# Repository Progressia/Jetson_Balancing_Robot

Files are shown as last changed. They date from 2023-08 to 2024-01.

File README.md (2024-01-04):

# JETSON BALANCING ROBOT

A two-wheeled balancing robot inspired by the [*SimpleFOC Balancing Robot*](https://github.com/simplefoc/Arduino-FOC-balancer.git)

<p align="center">
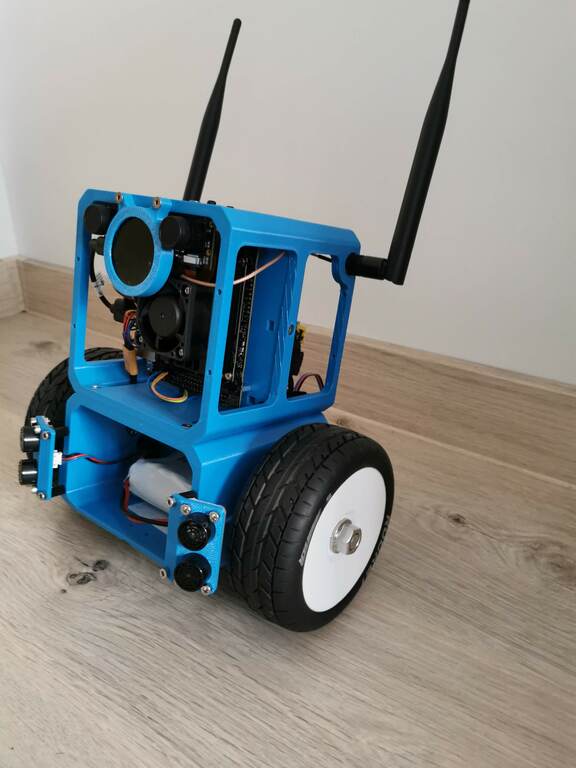
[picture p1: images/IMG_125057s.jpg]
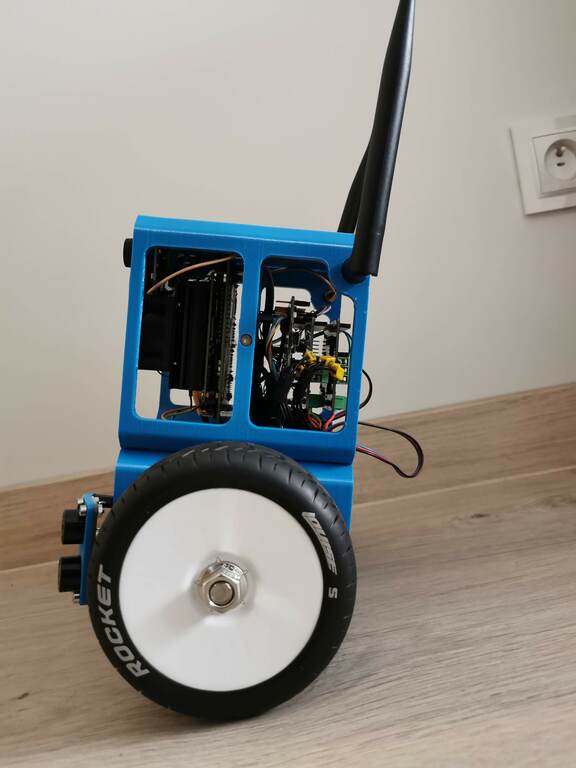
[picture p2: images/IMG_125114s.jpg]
  </p>

Modular two wheeled balancing robot based on gimbal BLDC motors and [*Simple**FOC**Shields*](https://simplefoc.com/). NVIDIA Jetson Nano is use  to allow for control motion on base computer vision algorithms and AI models. Application for remote control of robot was build on flutter framework. 3D models with STL files are in CAD folder.

## YouTube video demo

ToDo: Video -- comming soon

## Readme structure
- [Mechanical components](#mechanical-components)
    - [3D printed parts](#3d-printed-parts)
    - [Hardware parts](#hardware-parts)
- [Electrical components](#electrical-components)
    - [Structure](#structure)
    - [BLDC motor](#bldc-motor)
    - [Position sensors](#position-sensors)
    - [BLDC driver](#bldc-driver)
    - [IMU module](#imu-module)
    - [WiFi module](#wifi-module)
    - [Microcontroller](#microcontroller)
- [Software](#software)
    - [STM32 Code](#stm32-code)
    - [NVIDIA Jetson Nano Code](#nvidia-jetson-nano-code)
    - [Remote control app](#remote-control-app)
    - [RP2040 LCD UART](#rp2040-lcd-uart)

--------------------------

## Mechanical components

### 3D printed parts

Robot has 4 3d printed parts. You can find them in the `CAD` directory. They are (***reasonably precise***):
- Base frame (`base_frame.stl`)
- Cube frame (`cube_frame.stl`) 
- Plate for electronics (`plate.stl`)
- Wheel hub (`wheel_hub.stl`)
- Camera and LCD hub (`camera_lcd_hub.stl`)
- RP2040 LCD adapter (`rp2040_hub.stl`)
- Distance sensor hub (`dist_sens_hub.stl`)

Parts was printed from ABS filament.

>Beware: Assembly holes match the motor and electronics I was using, so please check the dimensions of your parts holes before printing

### Hardware parts

In addition to the printed parts, you will need two RC wheels (HEX17) and a handful of nuts and bolts

Component | Description
---- | ----
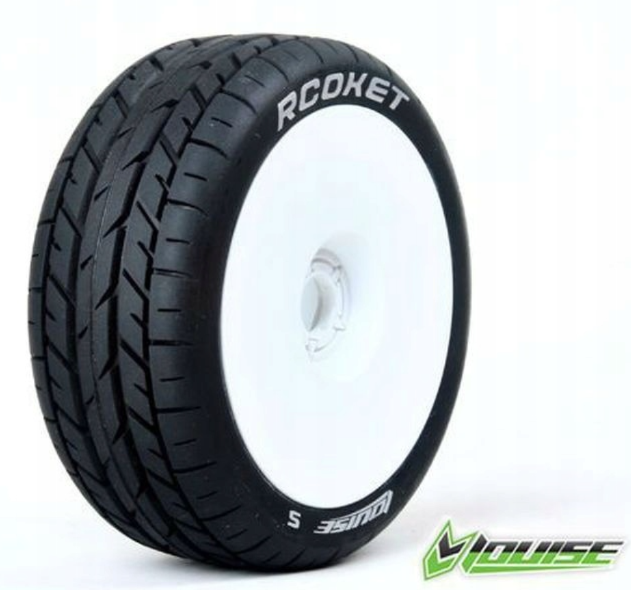
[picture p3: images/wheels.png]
 | Wheels Louise B-Rocket hex 17mm 1:8 Buggy (2 pcs)
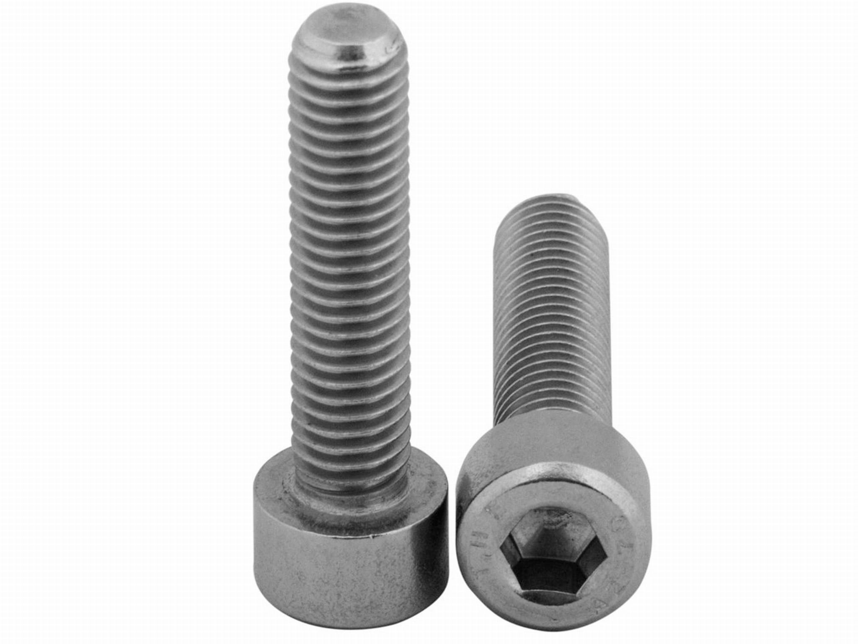
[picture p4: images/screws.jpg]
 | Screws M3x20 (4 pcs)
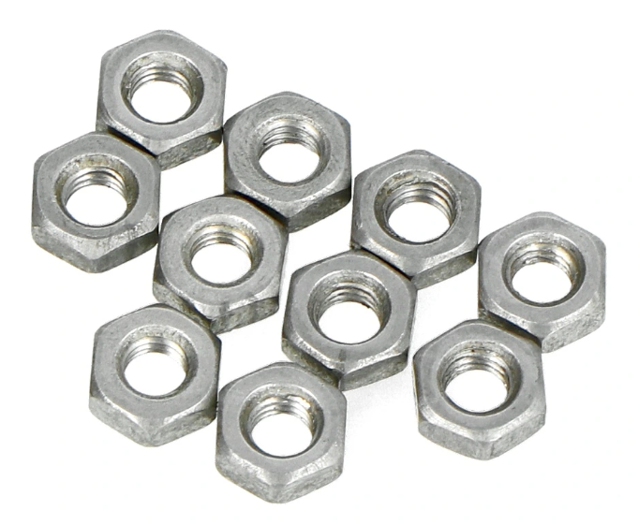
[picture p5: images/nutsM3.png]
 | Nuts M3 
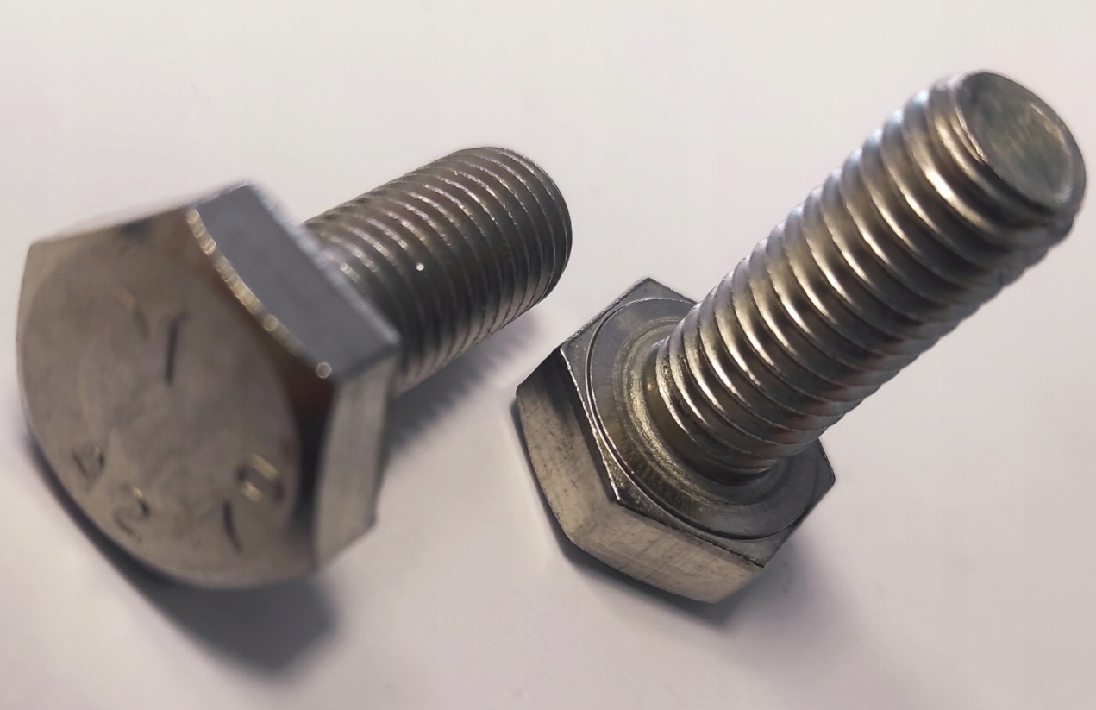
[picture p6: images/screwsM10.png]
 | Screws M10x25 (2 pcs)
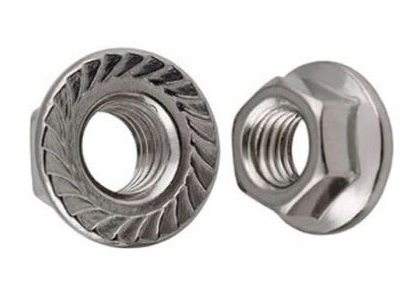
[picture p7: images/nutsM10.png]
  | Nuts M10 (2 pcs)

--------------------------

## Electrical components

### Structure
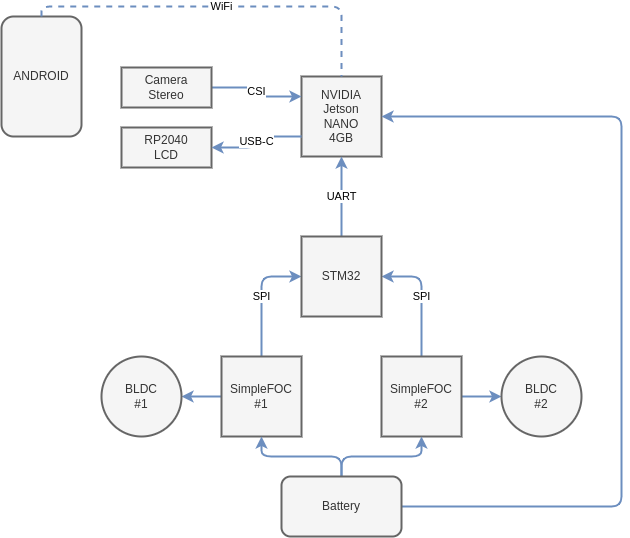
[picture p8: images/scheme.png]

<p style="text-align: center;">System diagram</p>

- Connection pinout

STM32 | SimpleFOC #1
---- | ----
5V | VCC
GND | GND

STM32 | SimpleFOC #2
---- | ----
5V | VCC
GND | GND

// (6, 5, 10, 8)
#define MOT1_A 6
#define MOT1_B 5
#define MOT1_C 10
#define MOT1_EN 8

// (9, 3, 11, 7)
#define MOT2_A 9
#define MOT2_B 3
#define MOT2_C 11
#define MOT2_EN 7

STM32 | IMU (MPU6050)
---- | ----
5V | VCC
PB8 (I2C1_SCL) | SCL
PB9 (I2C1_SDA) | SDA
GND | GND

STM32 | Magnetic Encoder #Left (AS5048A)
---- | ----
5V | VCC (Green)
PA10 (CS) | CS (White)
PB13 (SPI2_SCK) | CLK (Red)
PB15 (SPI2_MOSI) | MOSI (Black)
PB14 (SPI2_MISO) | MISO (Yellow)
GND | GND (Purple)

STM32 | Magnetic Encoder #Right (AS5048A)
---- | ----
5V | VCC (Green)
PB5 (CS) | CS (White)
PB13 (SPI2_SCK) | CLK (Red)
PB15 (SPI2_MOSI) | MOSI (Black)
PB14 (SPI2_MISO) | MISO (Yellow)
GND | GND (Purple)

STM32 | NVIDIA Jetson Nano 4GB
---- | ----
5V (optional) | 5V
PC11 (UART4_RX) | TXD (8-Yellow)
PC10 (UART4_TX) | RXD (10-Orange)
GND | GND (6)

NVIDIA Jetson Nano | RP2040 LCD
---- | ----
USB | USB-C
### BLDC motor

The BLDC motors I have used are the iPower GM4108. You can use any other gimbal motors of this class with minor modifications - repositioning the mounting holes in 3D printed parts.

Component | Description
---- | ----
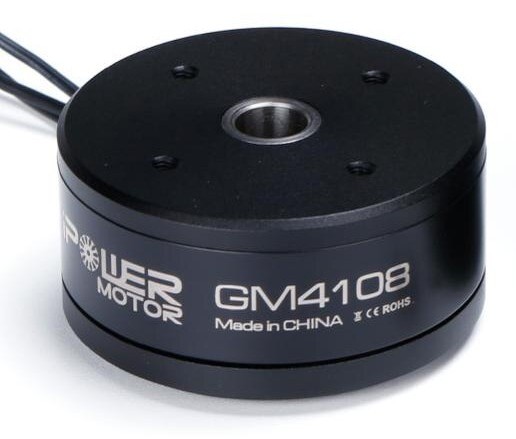
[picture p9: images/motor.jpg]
 | iPower Motor GM4108H-120T

### Position sensors
In my case, I used two magnetic sensors (attached to the motors). You can use any type of position sensor that is supported by the [*Simple**FOC**Shields library*](https://simplefoc.com/).

Component | Description
---- | ----
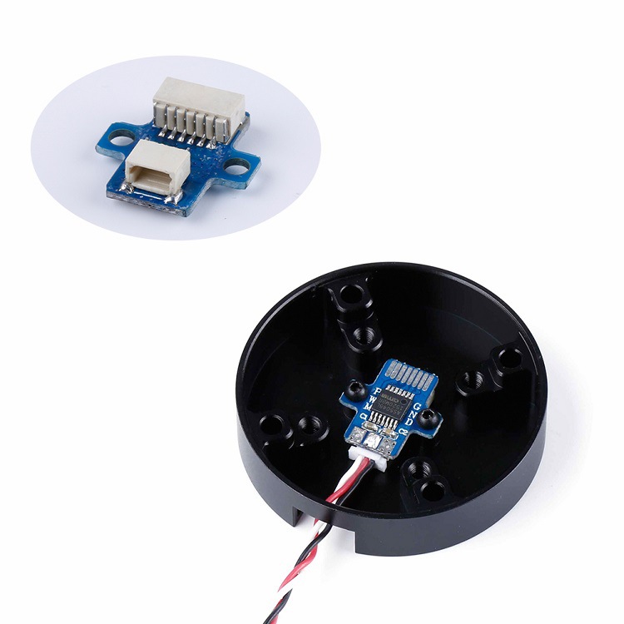
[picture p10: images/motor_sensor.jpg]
 | Magnetic sensor AS5048 (attached to the motors)

### BLDC driver
For this project, I used [*Simple**FOC**Shields v2.0.4*](https://simplefoc.com/), which enables the use of the FOC algorithm with BLDC motors.

Component | Description
---- | ----
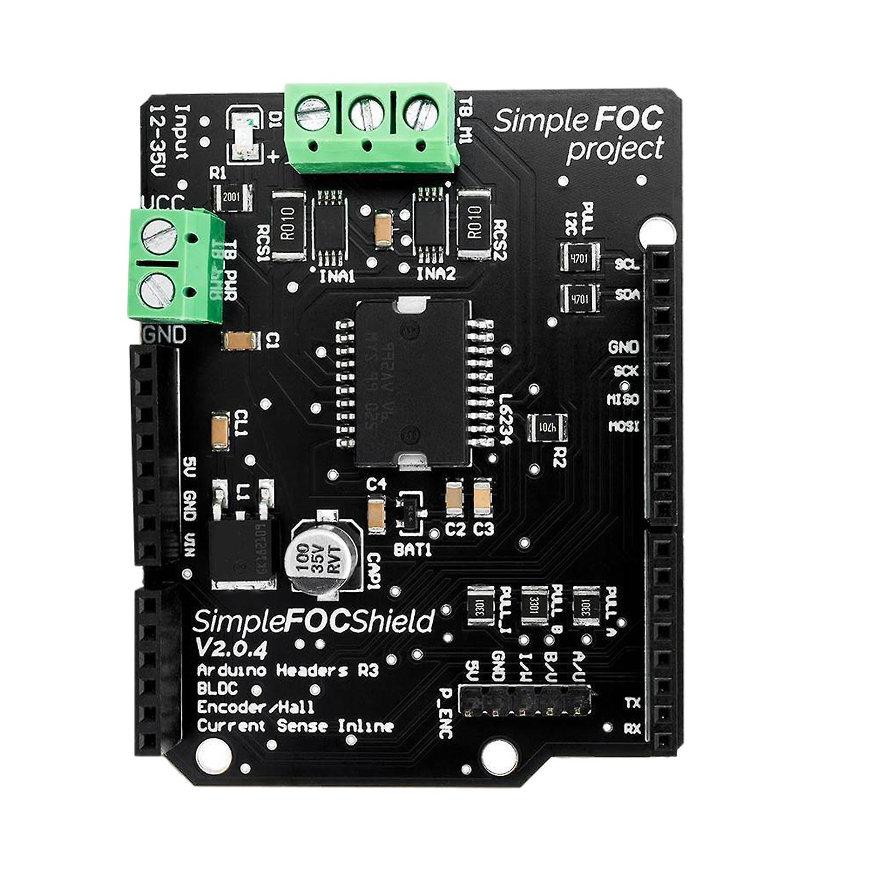
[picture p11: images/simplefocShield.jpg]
 | [SimpleFOC Shield v2.0.4](https://simplefoc.com/)

### IMU module
I used the IMU MPU6050 with integrated DMP.

Component | Description
---- | ----
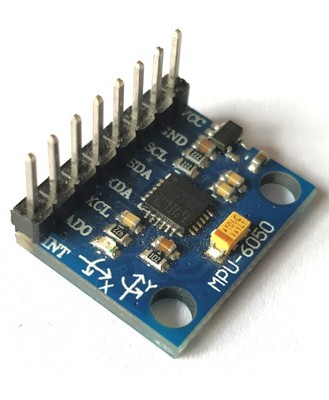
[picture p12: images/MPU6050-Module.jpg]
 | IMU MPU6050

### Embedded computing board & Microcontroller
Based on the [*SimpleFOC Balancing Robot*](https://github.com/simplefoc/Arduino-FOC-balancer.git), I decided to extend the robot and added mainly an NVIDIA Jetson Nano for using computer vision algorithms and an AI model.
I used the ESP8266 WiFi server for testing and initial calibration of the robot.

Component | Description
---- | ----
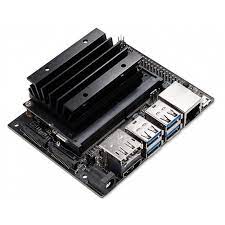
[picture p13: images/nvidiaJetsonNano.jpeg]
 | Nvidia Jetson Nano B01
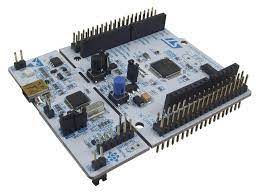
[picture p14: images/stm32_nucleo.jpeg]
 | STM32 F446 Nucleo
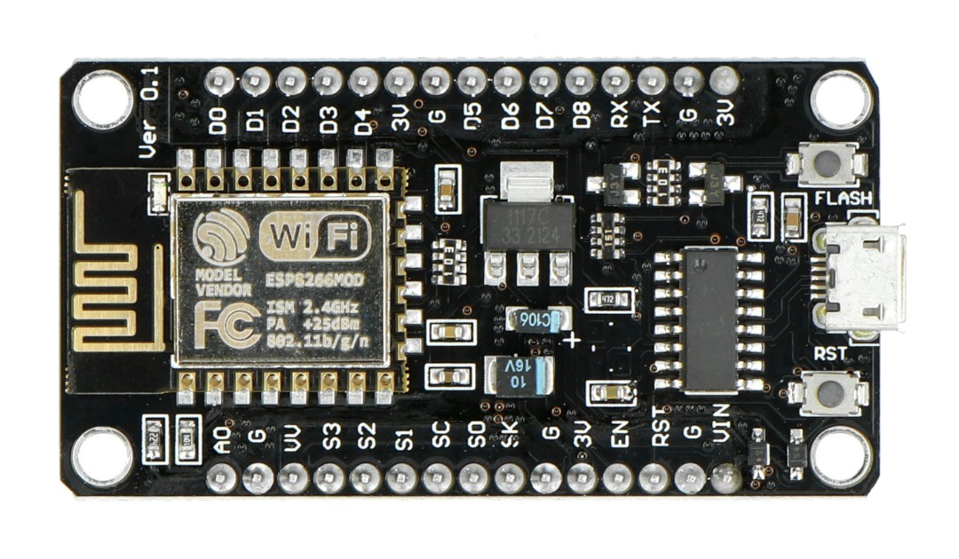
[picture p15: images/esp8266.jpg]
 | ESP8266
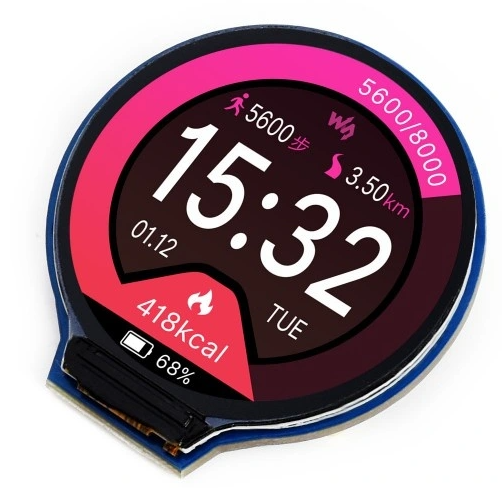
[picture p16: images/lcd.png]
 | [Waveshare RP2040 LCD IPS 1,28'' 240 x 240 px](https://www.waveshare.com/wiki/RP2040-LCD-1.28)

### Others
I added a camera, display and distance sensors. You can use any NVIDIA Jetson Nano compatible camera.

Component | Description
---- | ----
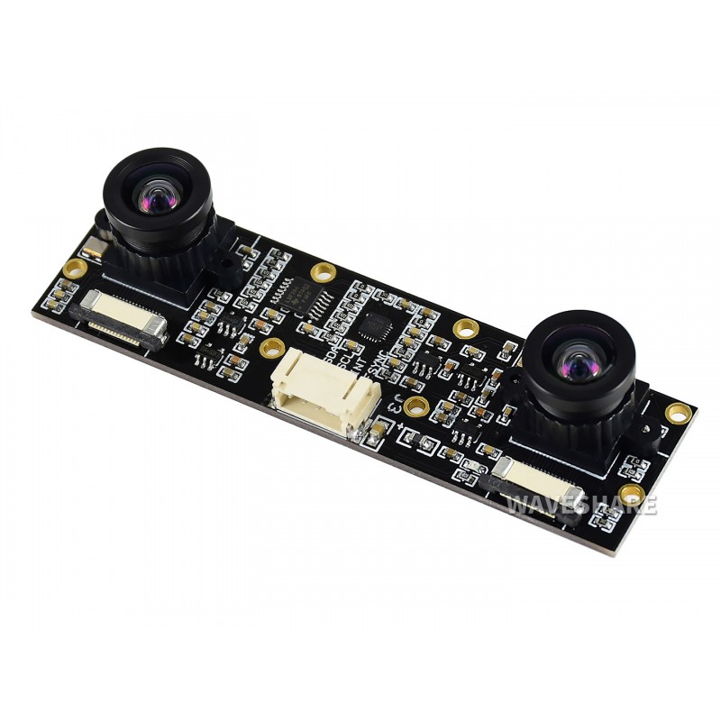
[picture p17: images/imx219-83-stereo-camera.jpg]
 | [IMX219-83 Stereo Camera](https://www.waveshare.com/wiki/IMX219-83_Stereo_Camera)
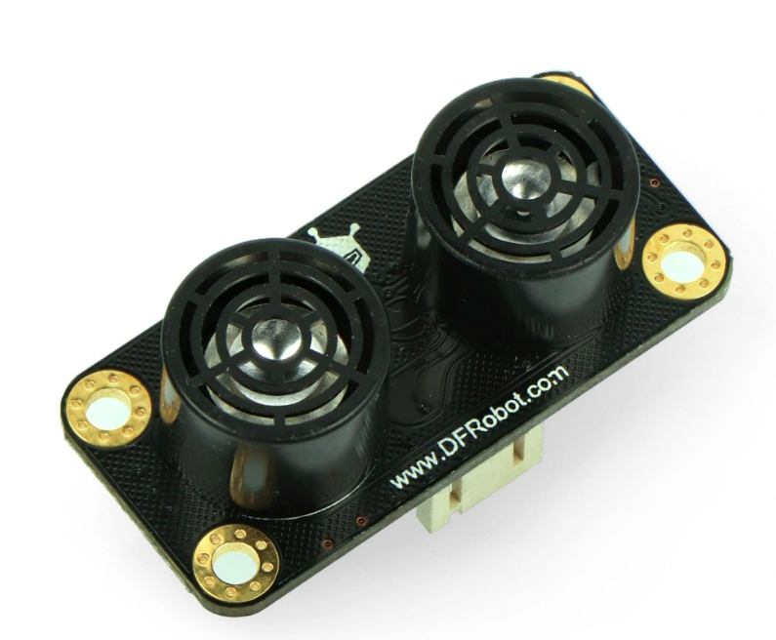
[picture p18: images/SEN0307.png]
 | [URM09 Analog Ultrasonic Sensor](https://www.dfrobot.com/product-1862.html) 2pcs
---| [Battery LiFePO4 9.9V 2500 mAh](https://btobattery.com/)

--------------------------

## Software

### STM32 Code
The code for the STM32 is actually almost the same as for the example [*SimpleFOC Balancing Robot*](https://github.com/simplefoc/Arduino-FOC-balancer.git) with a few modifications. 

For more details, see section [stm32_BLDC_Controller](https://github.com/Progressia/stm32_BLDC_Controller)

### NVIDIA Jetson Nano Code
As mentioned earlier. NVIDIA Jetson Nano is used to implement motion algorithms and implement AI models. As an example, it demonstrates how to get a remote view from a camera mounted on a robot and stream it to a smartphone. 

For more details, see section [nvidiaJetson_app](https://github.com/Progressia/Jetson_Balancing_Robot/tree/master/nvidiaJetson_app)

### Robot script
Script in Python with using object-oriented programming.

For more details, see section [RobotApp](https://github.com/Progressia/Jetson_Balancing_Robot/tree/master/RobotApp)

### Remote control app
I made the app to handle the robot's functions, parameter settings and camera view on the Flutter framework. You can compile the app on Android, iOS(not tested), Linux, Windows (not tested) and others. 

For more details, see section [flutter_remote_controller](https://github.com/Progressia/flutter_remote_jetson_controller)

### RP2040 LCD UART
The application, on the RP2040, displays information from the NVIDIA Jetson platform via the UART

For more details, see section [rp2040_lcd_uart](https://github.com/Progressia/RP2040_LCD_USB)

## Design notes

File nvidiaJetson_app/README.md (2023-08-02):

# NVIDIA Jetson App

Description - comming soon

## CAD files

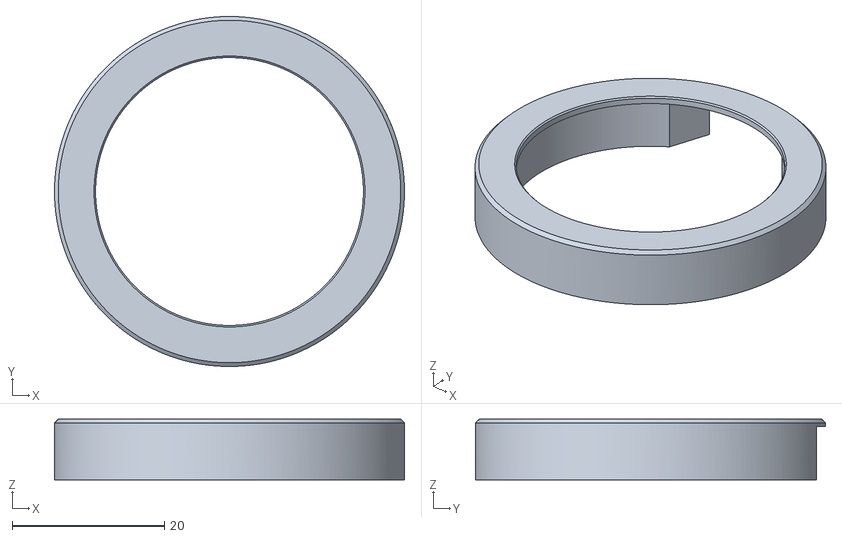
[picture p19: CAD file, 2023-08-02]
CAD/rp2040_hub.stl
46.0 x 46.0 x 8.00

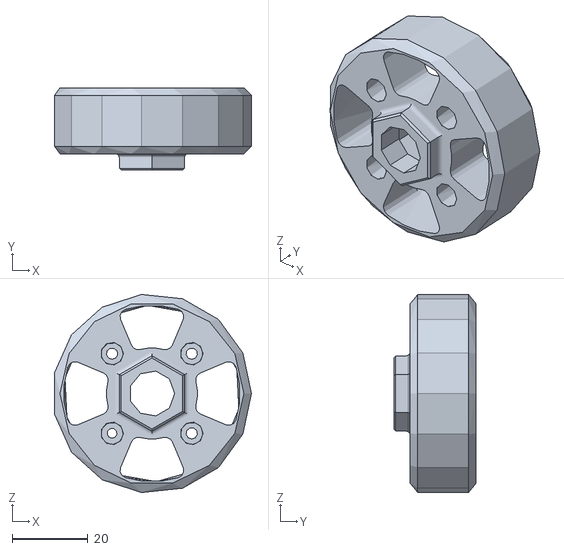
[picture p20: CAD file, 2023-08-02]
CAD/wheel_hub.stl
51.9 x 21.7 x 52.2

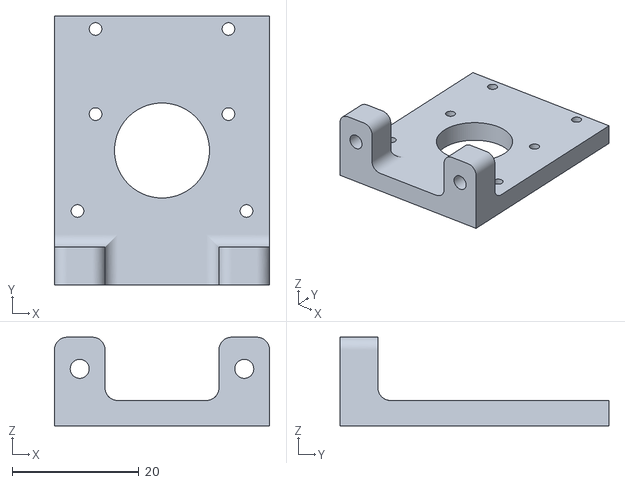
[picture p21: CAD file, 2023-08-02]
CAD/camera_lcd_hub.stl
34.0 x 42.5 x 14.0

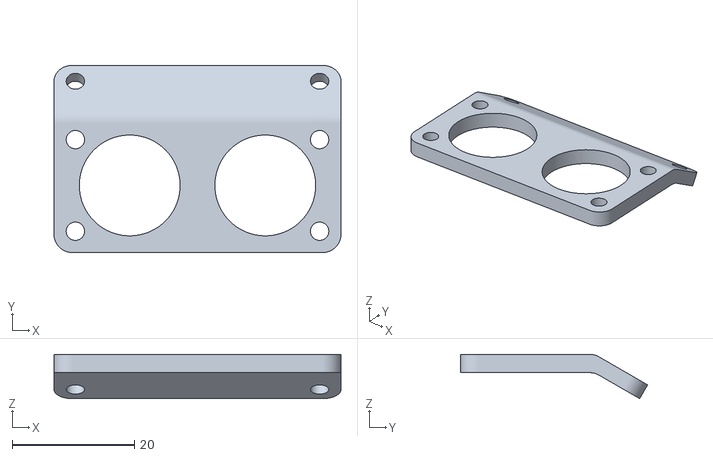
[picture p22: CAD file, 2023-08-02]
CAD/dist_sens_hub.stl
47.0 x 30.7 x 7.25

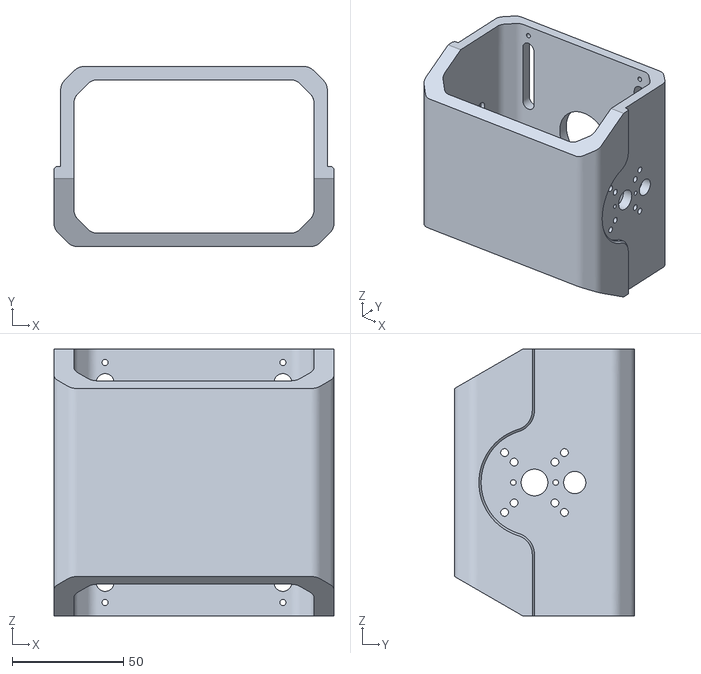
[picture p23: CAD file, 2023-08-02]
CAD/base_frame.stl
126.0 x 81.0 x 120.0

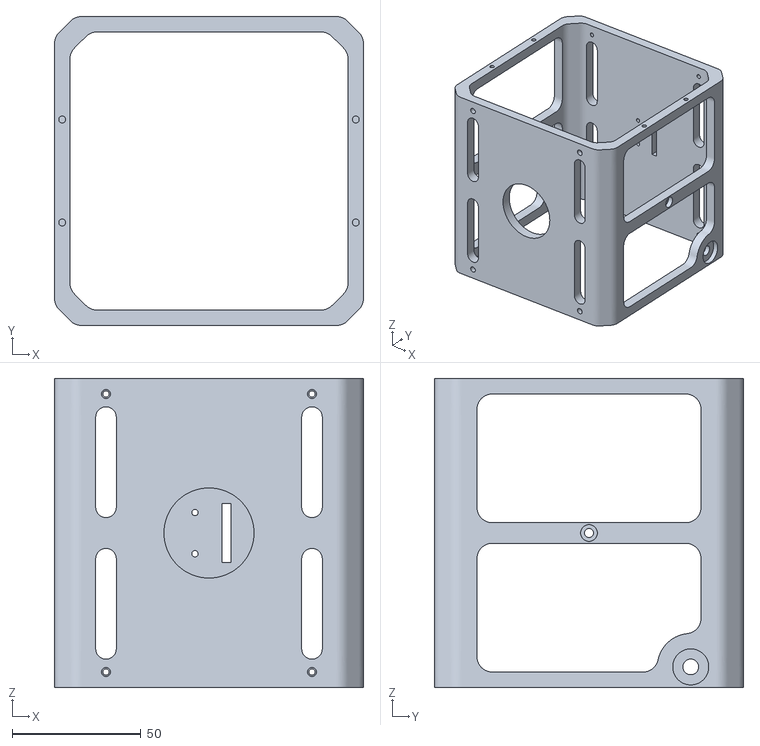
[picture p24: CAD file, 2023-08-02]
CAD/cube_frame.stl
120.0 x 120.0 x 120.0

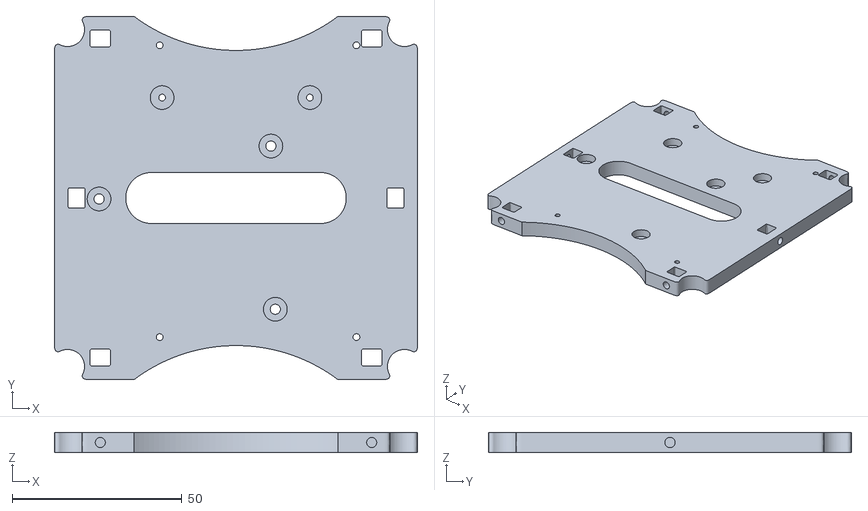
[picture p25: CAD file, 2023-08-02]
CAD/plate.stl
107.0 x 107.0 x 6.00

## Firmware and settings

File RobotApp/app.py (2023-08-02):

import robot
import time

import os
import json
from flask import Flask,request,jsonify
import threading

# ##################################################
data_string = ''
f = {}
f['O'] = '0'
f['T'] = '0'
f['S'] = '0'
f['M'] = '0'
f['V'] = '50'
f['D'] = '500'
f['X'] = '0'

up_comm = 0

def while_function():

    global data_string
    global up_comm
    i=0

    r = robot.Robot()
    time.sleep(2)

    r.ActiveRobot()
    time.sleep(2)
    print(r.getMotorsDriverInfo())
    time.sleep(2)
    r.DeactiveRobot()

    while True:
        
        # #######################################
        if(up_comm != 0):
            if(int(f['O']) == 1):
                r.active = 1
                r.ActiveRobot()
                print("Robot activated")
            if(int(f['O']) == 0):
                r.active = 0
                r.DeactiveRobot()
                print("Robot deactivated")
            up_comm = 0
        #######################################
        if (r.active == 1):
            if( (int(f['T']) != 0) or (int(f['S']) != 0) ):
            # Manual motion
                if( int(f['M']) == 0 ):
                    TLimit = int(f['T'])
                    SLimit = int(f['S'])
                    r.port.write(bytearray('T' + str(int(TLimit)) + '\n','ascii'))
                    r.port.write(bytearray('S' + str(int(SLimit)) + '\n','ascii'))
                # Automatic motions
                if( int(f['M']) > 0 ):
                    if(r.motion_state != 2):
                        r.motion(r, int(f['M']), int(f['V']), int(f['D']))
            else:
                r.stop_motors
                r.motion_state = 0
        # #######################################
        # Update parameters from Motors Driver
        if(i >= 20):
            data_string = r.getMotorsDriverInfo()
            i=0
        i += 1
        
        # Loop delay
        time.sleep(50/1000)
    # #######################################

# ###########################################
app = Flask(__name__)

# ###########################################
# API
@app.route('/api',methods=['GET', 'POST'])
def query_records():
    global f
    global up_comm
    
    if request.method == 'GET':
        if(request.args.get('Query')):
            d = {}
            d['Query'] = str(data_string)
            return jsonify(d)
    if request.method == 'POST':
        up_comm = 1
        # Active/Deactive
        if(request.args.get('O')):
            f['O'] = str(request.args.get('O'))
            print('O=' + f['O'])
            return jsonify(f)
        # Torque
        if(request.args.get('T')):
            f['T'] = str(request.args.get('T'))
            print('T=' + f['T'])
            return jsonify(f)
        # Steering
        if(request.args.get('S')):
            f['S'] = str(request.args.get('S'))
            print('S=' + f['S'])
            return jsonify(f)
        # Update
        if(request.args.get('U')):
            f['U'] = str(request.args.get('U'))
            print('U=' + f['U'])
            return jsonify(f)
        # Mode
        if(request.args.get('M')):
            f['M'] = str(request.args.get('M'))
            print('M=' + f['M'])
            return jsonify(f)
        # Velocity
        if(request.args.get('V')):
            f['V'] = str(request.args.get('V'))
            print('V=' + f['V'])
            return jsonify(f)
        # Duration
        if(request.args.get('D')):
            f['D'] = str(request.args.get('D'))
            print('D=' + f['D'])
            return jsonify(f)
        # AP (PID)
        if(request.args.get('AP')):
            f['AP'] = str(request.args.get('AP'))
            print(f['AP'])
            return jsonify(f)
        # AI (PID)
        if(request.args.get('AI')):
            f['AI'] = str(request.args.get('AI'))
            print(f['AI'])
            return jsonify(f)
        # AD (PID)
        if(request.args.get('AD')):
            f['AD'] = str(request.args.get('AD'))
            print(f['AD'])
            return jsonify(f)
        # A Ramp (PID)
        if(request.args.get('AR')):
            f['AR'] = str(request.args.get('AR'))
            print(f['AR'])
            return jsonify(f)
        # A Limit (PID)
        if(request.args.get('AL')):
            f['AL'] = str(request.args.get('AL'))
            print(f['AL'])
            return jsonify(f)
        # BP (PID)
        if(request.args.get('BP')):
            f['BP'] = str(request.args.get('BP'))
            print(f['BP'])
            return jsonify(f)
        # BI (PID)
        if(request.args.get('BI')):
            f['BI'] = str(request.args.get('BI'))
            print(f['BI'])
            return jsonify(f)
        # BD (PID)
        if(request.args.get('BD')):
            f['BD'] = str(request.args.get('BD'))
            print(f['BD'])
            return jsonify(f)
        # B Ramp (PID)
        if(request.args.get('BR')):
            f['BR'] = str(request.args.get('BR'))
            print(f['BR'])
            return jsonify(f)
        # B Limit (PID)
        if(request.args.get('BL')):
            f['BL'] = str(request.args.get('BL'))
            print(f['BL'])
            return jsonify(f)
        # Pitch filter
        if(request.args.get('CF')):
            f['CF'] = str(request.args.get('CF'))
            print(f['CF'])
            return jsonify(f)
        # Steering filter
        if(request.args.get('DF')):
            f['DF'] = str(request.args.get('DF'))
            print(f['DF'])
            return jsonify(f)
        # Throttle filter
        if(request.args.get('EF')):
            f['EF'] = str(request.args.get('EF'))
            print(f['EF'])
            return jsonify(f)
        # Close system
        if(request.args.get('X')):
            f['X'] = str(request.args.get('X'))
            print('X=' + f['X'])
            os.system('systemctl poweroff')
            return jsonify(f)
# ###########################################
def run_app():
    # app.run(debug=False, threaded=True)
    app.run(host='192.168.43.70', port=5000, debug=False, threaded=True)
# ###########################################

# ###########################################
if __name__ == '__main__':
    first_thread = threading.Thread(target=run_app)
    second_thread = threading.Thread(target=while_function)
    first_thread.start()
    second_thread.start()
# ###########################################

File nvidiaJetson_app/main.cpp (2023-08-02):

#include <unistd.h>
#include <stdio.h>
#include <chrono>
#include <uart.hpp>

#include <stdlib.h>

#include <cstdio>
#include <iostream>
#include <memory>
#include <stdexcept>
#include <string>
#include <array>

using namespace std;
using namespace std::chrono;

using namespace UART;

char buff[30];
int n=0;

void testUART(Uart u)
{
    std::string CMDbuff = "";

    CMDbuff = "O1";
    n = sprintf(buff, "%s\n", CMDbuff.c_str());
    u.sendUart((uint8_t *)buff, n);
    usleep(2000000);

    CMDbuff = "O0";
    n = sprintf(buff, "%s\n", CMDbuff.c_str());
    u.sendUart((uint8_t *)buff, n);
    usleep(2000000);
}

std::string exec(const char *cmd)
{
    std::array<char, 128> buffer;
    std::string result;
    std::unique_ptr<FILE, decltype(&pclose)> pipe(popen(cmd, "r"), pclose);
    if (!pipe)
    {
        throw std::runtime_error("popen() failed!");
    }
    while (fgets(buffer.data(), buffer.size(), pipe.get()) != nullptr)
    {
        result += buffer.data();
    }
    return result;
}

int rx_i = 0;

int main(int argc, char **argv)
{

    usleep(2000000);

    Uart u;
    uint8_t m[256];
    int comm_state = 0;

    int i = 0;
    
    system("../connect_WiFi.sh");
    usleep(50000000);

    system("python3 /home/nano/VSCode_Projects/RobotApp/app.py &");
    usleep(50000000);
    // -- Run camera stream by RTP (Using gstreamer)
    system("gst-launch-1.0 nvarguscamerasrc sensor-id=0 ! 'video/x-raw(memory:NVMM), format=NV12, width=1280, height=720' ! nvvidconv flip-method=0 ! nvv4l2h264enc insert-sps-pps=true ! h264parse ! rtph264pay pt=96 ! udpsink host=100.127.21.101 port=5001 &");

    while (true)
    {

        std::string IPbuff = exec("hostname -I");
        // std::cout << IPbuff;

        std::string strFirst = IPbuff.substr(0, IPbuff.find(' '));
        IPbuff = strFirst;
        // std::cout << IPbuff << std::endl;

        n = sprintf(buff, "IP:%s\n", IPbuff.c_str());

        u.sendUart((uint8_t *)buff, n);
        usleep(10000000);
    }

    return 0;
}

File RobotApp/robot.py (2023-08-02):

import serial
import time
import atexit

class Robot:
    port = serial.Serial('/dev/ttyTHS1',115200, timeout=1)
    time.sleep(1)
    active = 0

    motion_state = 0
    motion_start = 0
    motion_end = 0

    def __init__(self):

        # Initialize drivers BLDC
        self.MotorsDriver = Motors(Robot.port)
        time.sleep(2)

        # Local variable for each motor
        self.left_motor = self.MotorsDriver.getMotor(1)
        self.right_motor = self.MotorsDriver.getMotor(2)

        # Stop motors if app stopped
        atexit.register(self.DeactiveRobot)

    def motion(self, motion, speed, duration):
        STRAIGHT = 1
        TURN_LEFT = 2
        TURN_RIGHT = 3
        SPIN_LEFT = 4
        SPIN_RIGHT = 5
        
        # INIT
        if (self.motion_state == 0):
            self.motion_start = time.time()
            self.motion_state = 1
        # START
        elif (self.motion_state == 1):

            if motion == STRAIGHT:
                self.straight(speed)
            if motion == TURN_LEFT:
                self.turn_left(speed)
            if motion == TURN_RIGHT:
                self.turn_right(speed)
            if motion == SPIN_LEFT:
                self.spin_left(speed)
            if motion == SPIN_RIGHT:
                self.spin_right(speed)

            self.motion_end = time.time()
            if( (self.motion_end-self.motion_start) > (duration/1000)):
                self.motion_state = 2
                self.motion_start = time.time()
        # STOP
        elif (self.motion_state == 3):
            # Need fix - brake with adjustable power
            # self.brake_motion(self, motion, (-1)*speed, 2)
            self.stop_motors

    def straight(self, speed):
        self.left_motor.setSpeed((-1)*speed)
        self.right_motor.setSpeed((-1)*speed)
        self.MotorsDriver.run(Motors.START)
        print("Go straight")

    def turn_left(self, speed):
        self.left_motor.setSpeed(0)
        self.right_motor.setSpeed((-1)*speed)
        self.MotorsDriver.run(Motors.START)
        print("Turn left")

    def turn_right(self, speed):
        self.left_motor.setSpeed((-1)*speed)
        self.right_motor.setSpeed(0)
        self.MotorsDriver.run(Motors.START)
        print("Turn right")

    def spin_left(self, speed):
        self.left_motor.setSpeed((-1)*speed)
        self.right_motor.setSpeed(speed)
        self.MotorsDriver.run(Motors.START)
        print("Spin left")

    def spin_right(self, speed):
        self.left_motor.setSpeed(speed)
        self.right_motor.setSpeed((-1)*speed)
        self.MotorsDriver.run(Motors.START)
        print("Spin right")

    def stop_motors(self):
        self.left_motor.setSpeed(0)
        self.right_motor.setSpeed(0)
        self.MotorsDriver.run(Motors.RELEASE)

    def ActiveRobot(self):
        cmd = "O1"
        for i in range(3):
            print("Tx: " + self.sendCmdRobot(cmd))
            response = self.readline()
            print("Rx: " + str(response))
            print("Test: " + self.compareTxRx(cmd, response))
            if response != "Timeout":
                break
    
    def DeactiveRobot(self):
        cmd = "O0"
        for i in range(3):
            print("Tx: " + self.sendCmdRobot(cmd))
            response = self.readline()
            print("Rx: " + str(response))
            print("Test: " + self.compareTxRx(cmd, response))
            if response != "Timeout":
                break

    def getMotorsDriverInfo(self):
        data = ""
        print("Tx: " + self.sendCmdRobot("U0"))
        self.paramU0 = self.readline()
        print("Rx: " + self.paramU0)

        print("Tx: " + self.sendCmdRobot("G0"))
        self.paramG0 = self.readline()
        print("Rx: " + self.paramG0)
        data = f"{self.paramU0}" + f"{self.paramG0}" + "}"
        return data

    def TestUartActiveDeactiveRobot(self, tim):
        print("TestUartActiveDeactiveRobot ...")
        for i in range(2):
            self.ActiveRobot()
            time.sleep(tim)
            self.DeactiveRobot()
            time.sleep(tim)

    def Test_CMD_Robot(self, cmd, value, tim):
        print("Test_CMD_Robot ...")
        response = ""
        for i in range(2):
            # 1
            self.ActiveRobot()
            # 2
            print("Tx: " + self.sendCmdRobot(cmd + str(value)))
            response = self.readline()
            print("Rx: " + str(response))
            print("Test: " + self.compareTxRx(str(value), str(int(float(response)))))
            time.sleep(tim)
            # 3
            print("Tx: " + self.sendCmdRobot(cmd + str(0)))
            response = self.readline()
            print("Rx: " + str(response))
            print("Test: " + self.compareTxRx(str(0), str(int(float(response)))))
            time.sleep(tim)
            # 4
            self.DeactiveRobot()

    def Test_Response_Robot(self, cmd, tim):
        print("Test_Response_Robot ...")
        response = ""
        for i in range(2):
            # 1
            self.ActiveRobot()
            # 2
            print("Tx: " + self.sendCmdRobot(cmd))
            response = self.readline()
            print("Rx: " + str(response))
            time.sleep(tim)
            # 3
            print("Tx: " + self.sendCmdRobot(cmd))
            response = self.readline()
            print("Rx: " + str(response))
            time.sleep(tim)
            # 4
            self.DeactiveRobot()

    def sendCmdRobot(self, data):
        self.port.write(bytearray(data + '\n','ascii'))
        return bytearray(data,'ascii').decode("utf-8")

    def readline(self):
        message = ""
        data = ""
        while True:
            data = self.port.read()
            if data == b'':
                message = "Timeout" # 1 s
                break
            if data == b'\n':
                break
            message += str(data.decode("utf-8") )
        return message

    def compareTxRx(self, tx, rx):
        ret = ""
        if(tx == rx):
            ret = rx + " --> OK!"
        else:
            ret = " --> Fail"
        return ret

class BLDC_Motor:
    def __init__(self, num):
        self.speed = 0
        self.motornum = num

    def setSpeed(self, speed):
        if (speed < -100):
            speed = -100
        if (speed > 100):
            speed = 100
        self.speed = speed
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
